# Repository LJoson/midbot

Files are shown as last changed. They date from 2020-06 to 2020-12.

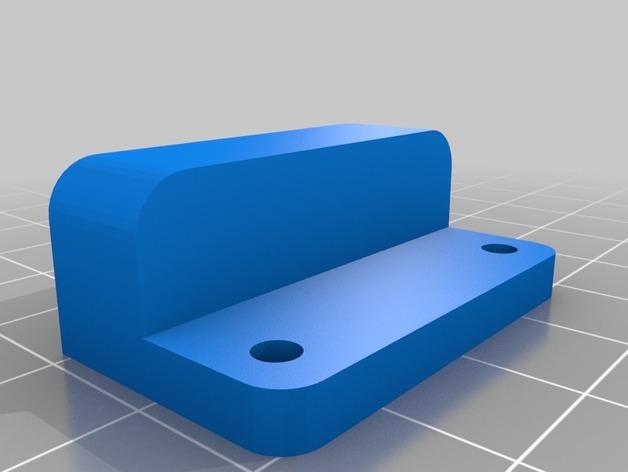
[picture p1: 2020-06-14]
midTbot/images/e1dbb92214a00844d0065ffd1623967f_preview_featured.jpg

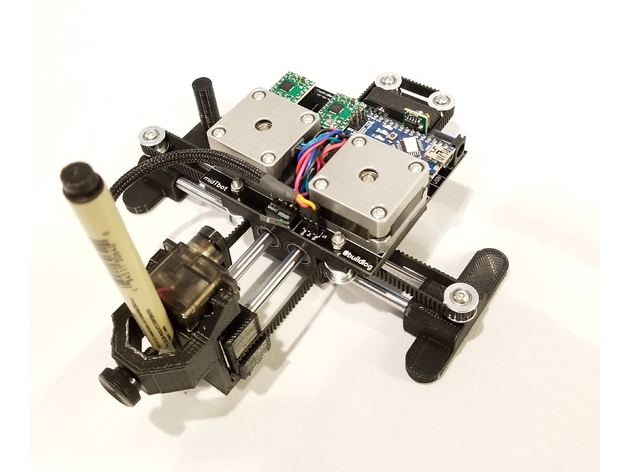
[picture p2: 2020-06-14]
midTbot打印件图纸.jpg

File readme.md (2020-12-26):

# 灵魂画手

## 结构
现在市面上有很多结构的写字机，而我要介绍的是经典的corexy结构的写字机。该写字机是基于T站上一个开源[写字机项目](https://www.thingiverse.com/thing:2587684).其结构如图：


<br/>
一般的corexy十字架构写字机两个电机是分开，其不好的一点就是太占空间，而midbot将两个控制电机集中在了中间，极大节省了空间。
另外想补充的是在我diy的过程中也发现几点可改进的地方
 - （1）底部支撑：不稳，容易倒
- （2）舵机抬笔：卡同步带地方易断裂,可以控制填充度，不易断裂或者改结构

## 工具
T站上控制主板多是esp32以及arduino nano,我使用的是arduino uno+cnc sheild控制器，控制算法就是经典的GRBL，网络上也有在stm32上移植grbl,我还没有实现，后面实现了进行补充。

所有资料获取：[https://github.com/LJoson/midbot](https://github.com/LJoson/midbot)

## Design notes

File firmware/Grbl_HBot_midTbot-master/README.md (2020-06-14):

# Grbl CNC for the MidTBot

This is a fork of Grbl 1.1f for the MidTBot. 

midTbot

The official Grbl Repo by Sungeon Jeon is [https://github.com/gnea/grbl](https://github.com/gnea/grbl).

This fork turns on the CoreXY functions, sets the correct defaults and adds pen up/down control of a hobby servo for the pen.

Any work coordinate system Z>0 is pen up. Any work coordinate system Z<=0 is pen down.

The MidTBot is documented on the [http://www.buildlog.net/blog/?s=midtbot](http://www.buildlog.net/blog/?s=midtbot). Please ask all question on the blog.

Note: This needs to be installed as an Arduino library.  See the [Grbl wiki pages](https://github.com/gnea/grbl/wiki/Compiling-Grbl) on how to do that.

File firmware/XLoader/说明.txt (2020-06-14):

本程序是吧PN（winAVR）编译成的  Grbl.hex   文件导入arduino的

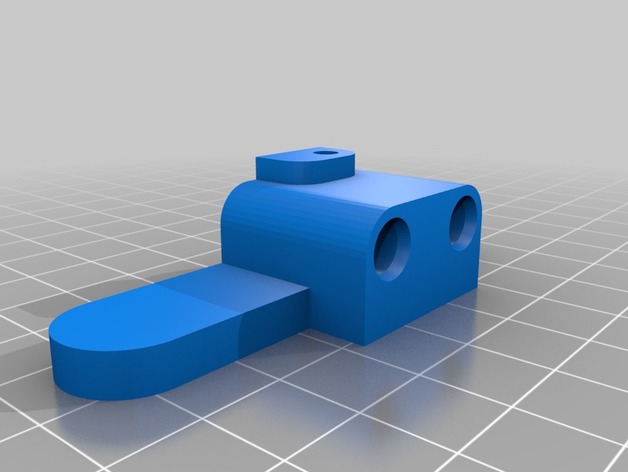
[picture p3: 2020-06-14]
midTbot/images/b2f7f5a82af39902b7f8d88fb1b9a30f_preview_featured.jpg

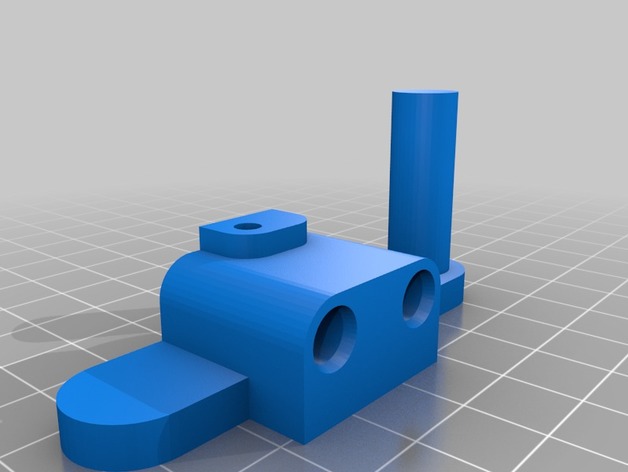
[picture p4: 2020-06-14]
midTbot/images/ceb36d84fa22627349a421942579ca87_preview_featured.jpg

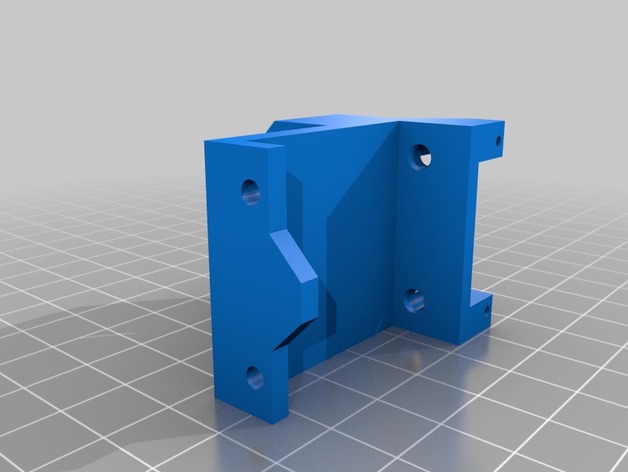
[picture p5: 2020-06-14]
midTbot/images/2167c671efe35847824a021b72f78122_preview_featured.jpg

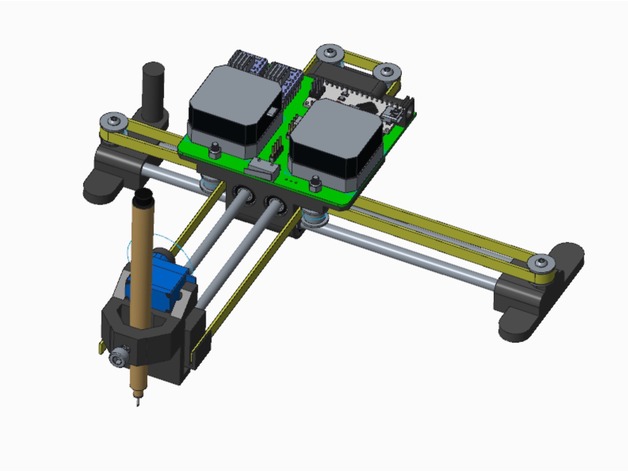
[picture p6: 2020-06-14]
midTbot/images/1ea54ba4b695a37cefbbd15caf575798_preview_featured.jpg

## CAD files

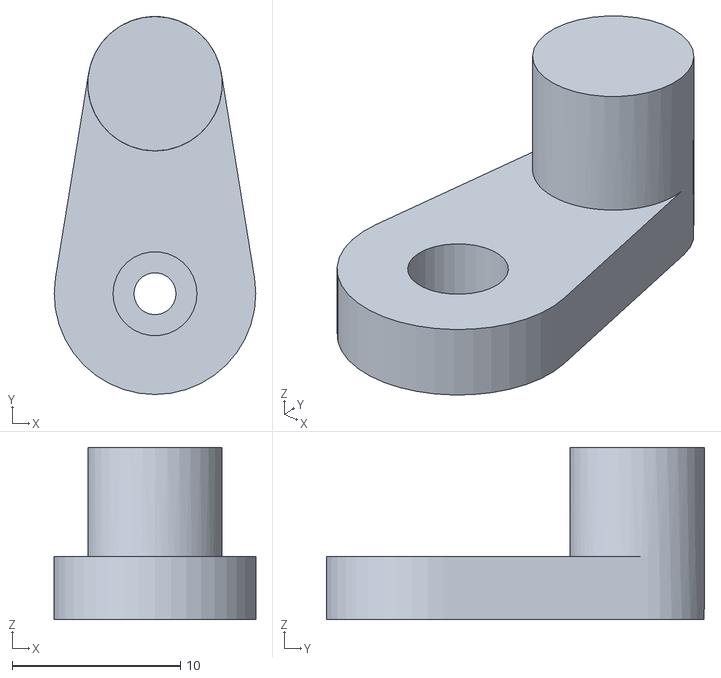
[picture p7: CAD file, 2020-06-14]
midTbot/files/midt_pen_lift_cam.stl
12.0 x 22.5 x 10.2

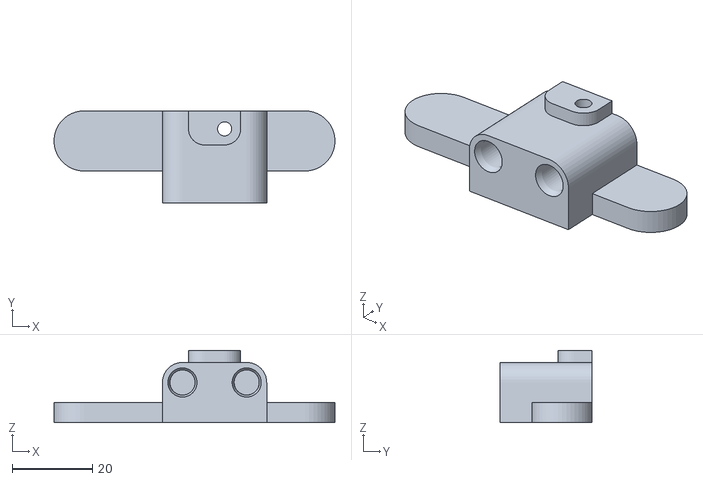
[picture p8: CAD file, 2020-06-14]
midTbot/files/midt_right_foot.stl
70.0 x 23.0 x 18.0

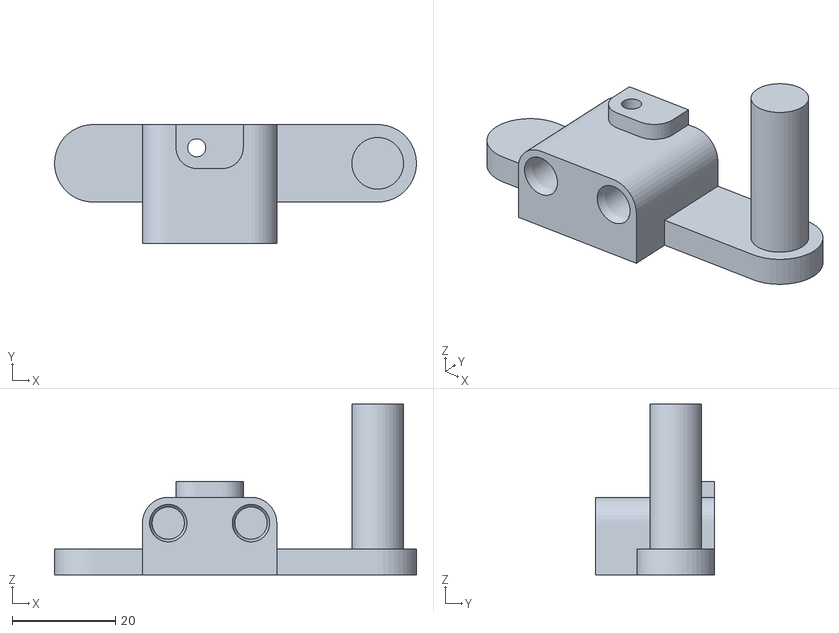
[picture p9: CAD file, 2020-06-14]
midTbot/files/midt_left_foot.stl
70.0 x 23.0 x 33.0

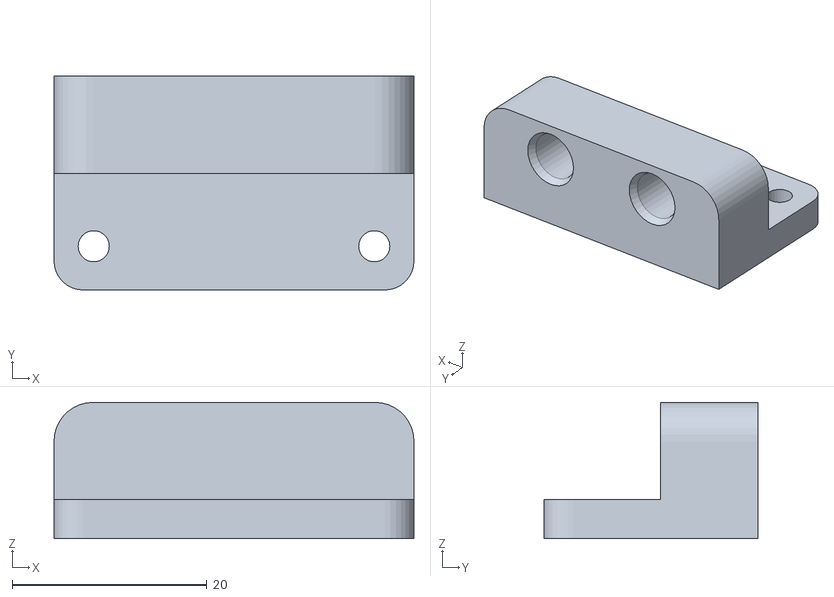
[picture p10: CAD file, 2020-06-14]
midTbot/files/midt_tailblock.stl
37.0 x 22.0 x 14.0

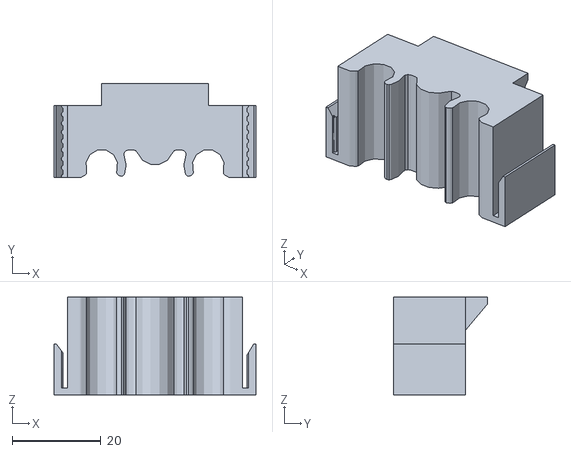
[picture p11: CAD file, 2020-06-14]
midTbot/files/midt-headblock.stl
45.5 x 21.2 x 22.0

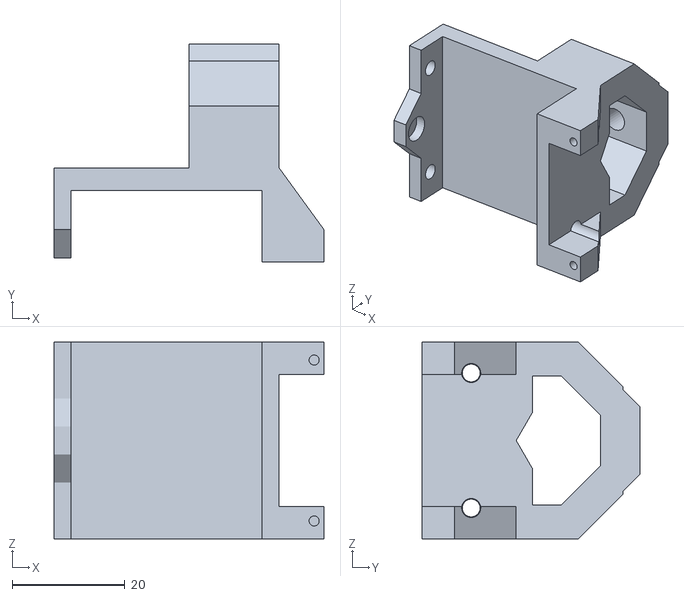
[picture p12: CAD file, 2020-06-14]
midTbot/files/midtbot_pen_carriage.stl
48.0 x 38.8 x 35.0

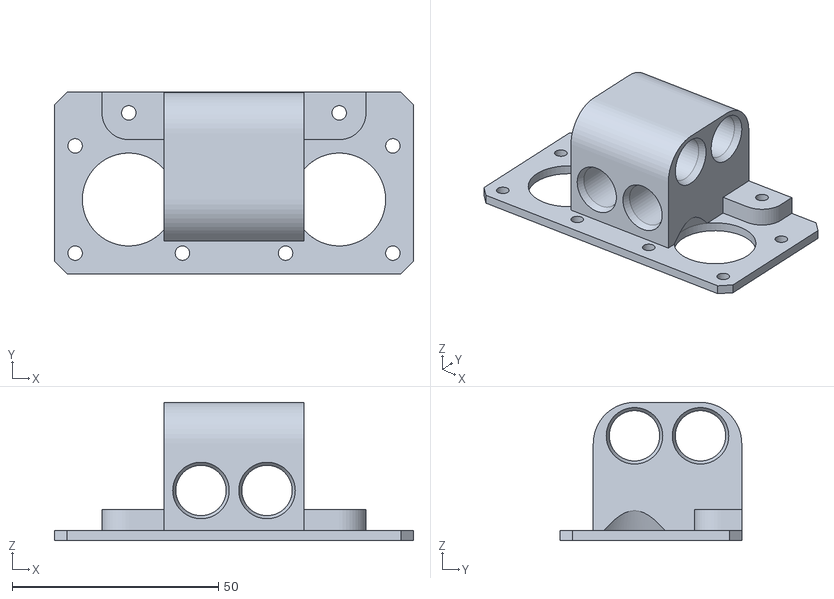
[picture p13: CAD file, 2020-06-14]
midTbot/files/midt_carriage_block.stl
87.0 x 44.0 x 33.5

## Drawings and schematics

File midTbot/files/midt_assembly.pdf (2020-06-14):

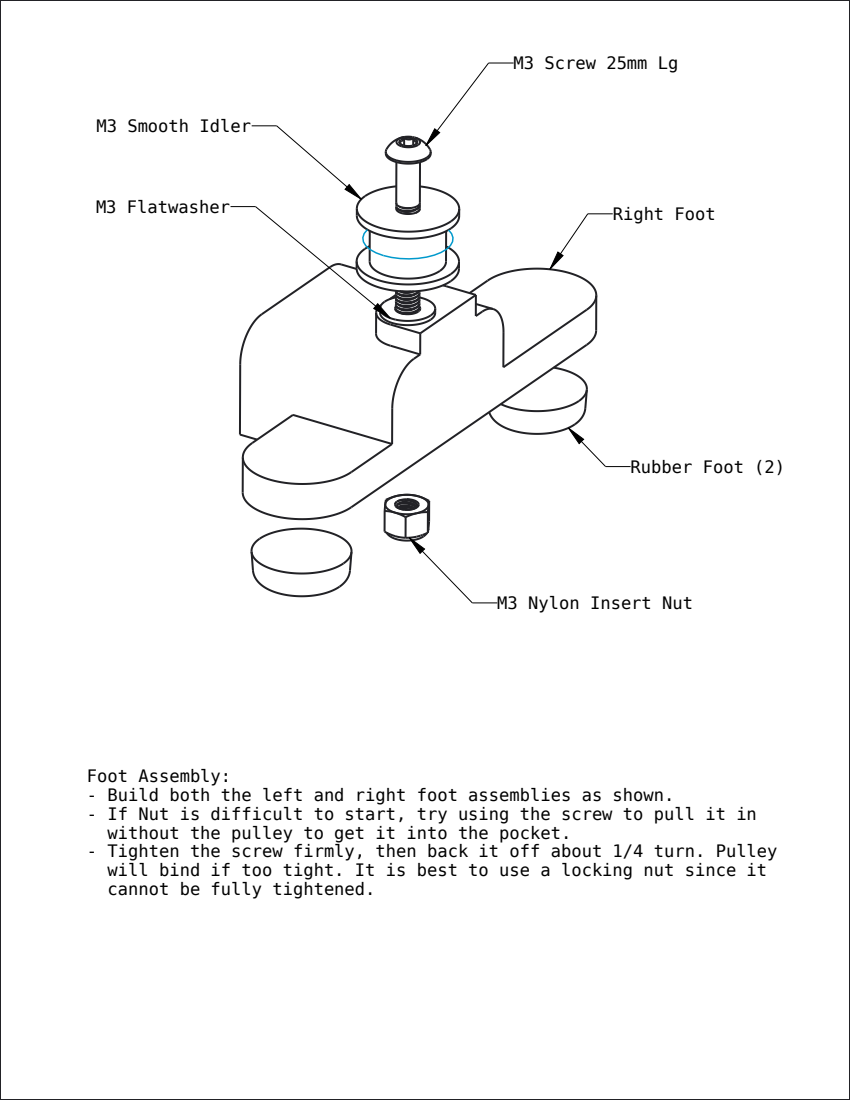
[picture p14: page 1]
Rubber Foot (2); M3 Screw 25mm Lg; M3 Smooth Idler

Right Foot M3 Flatwasher

M3 Nylon Insert Nut

Foot Assembly:
- Build both the left and right foot assemblies as shown.
- If Nut is difficult to start, try using the screw to pull it in
without the pulley to get it into the pocket.
- Tighten the screw firmly, then back it off about 1/4 turn. Pulley
will bind if too tight. It is best to use a locking nut since it
cannot be fully tightened.

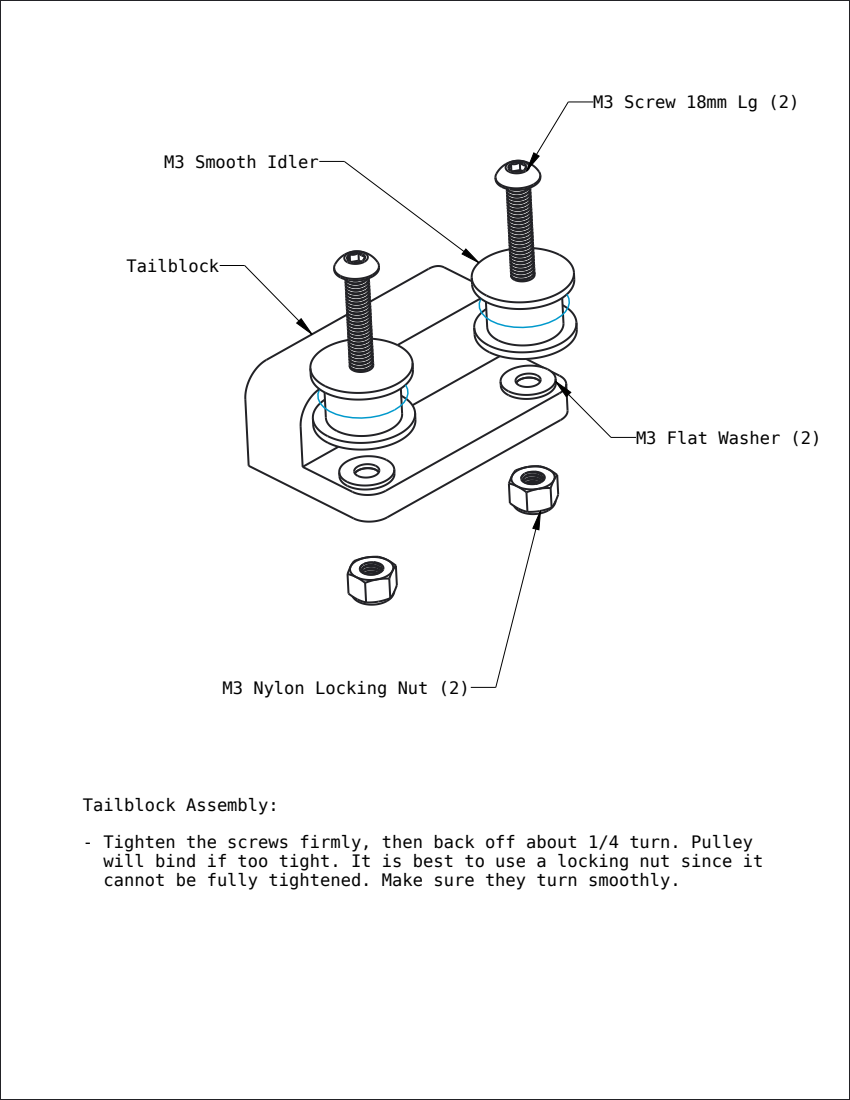
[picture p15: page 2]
Tailblock; M3 Screw 18mm Lg (2); M3 Flat Washer (2); M3 Smooth Idler

M3 Nylon Locking Nut (2)

Tailblock Assembly:
- Tighten the screws firmly, then back off about 1/4 turn. Pulley
will bind if too tight. It is best to use a locking nut since it
cannot be fully tightened. Make sure they turn smoothly.

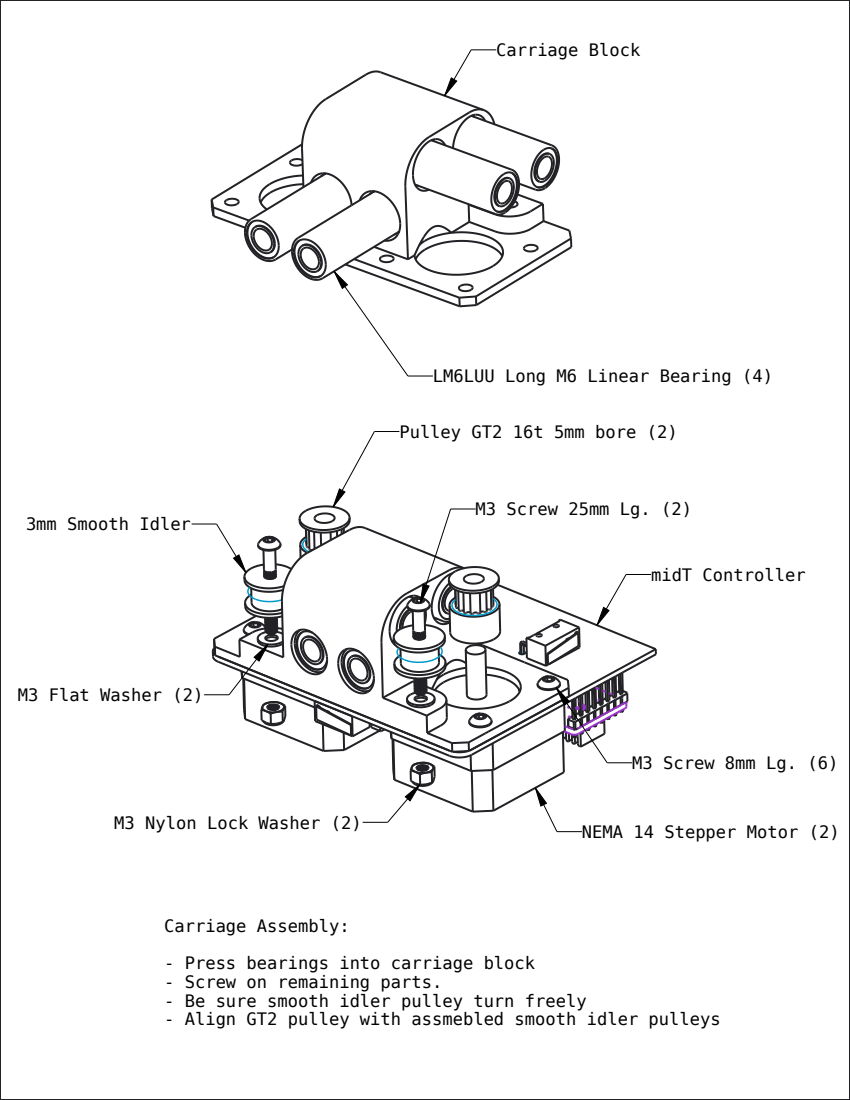
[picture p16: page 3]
Carriage Block; midT Controller; Pulley GT2 16t 5mm bore (2); 3mm Smooth Idler; M3 Flat Washer (2); M3 Screw 25mm Lg. (2); M3 Screw 8mm Lg. (6)

LM6LUU Long M6 Linear Bearing (4)

M3 Nylon Lock Washer (2)

NEMA 14 Stepper Motor (2)

Carriage Assembly:
- Press bearings into carriage block
- Screw on remaining parts.
- Be sure smooth idler pulley turn freely
- Align GT2 pulley with assmebled smooth idler pulleys

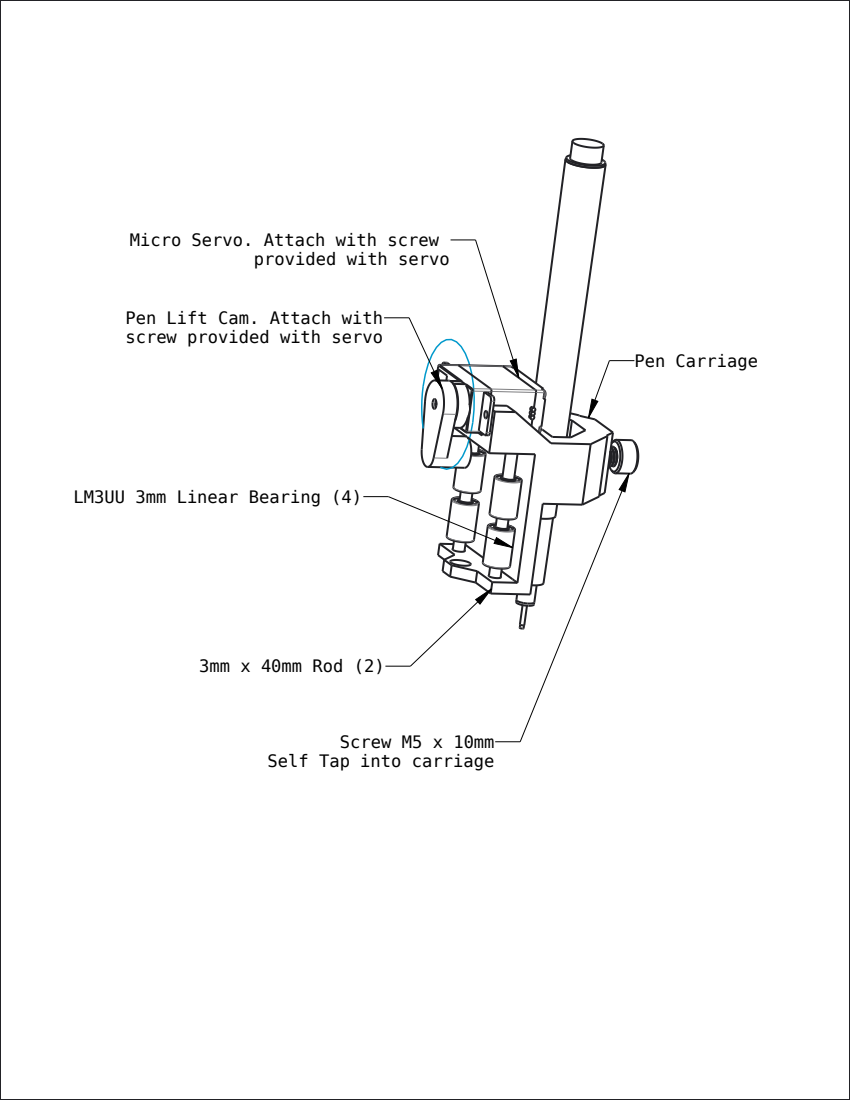
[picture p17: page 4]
Pen Carriage; 3mm x 40mm Rod (2); LM3UU 3mm Linear Bearing (4); Screw M5 x 10mm

Micro Servo. Attach with screw

provided with servo

Pen Lift Cam. Attach with
screw provided with servo

Self Tap into carriage

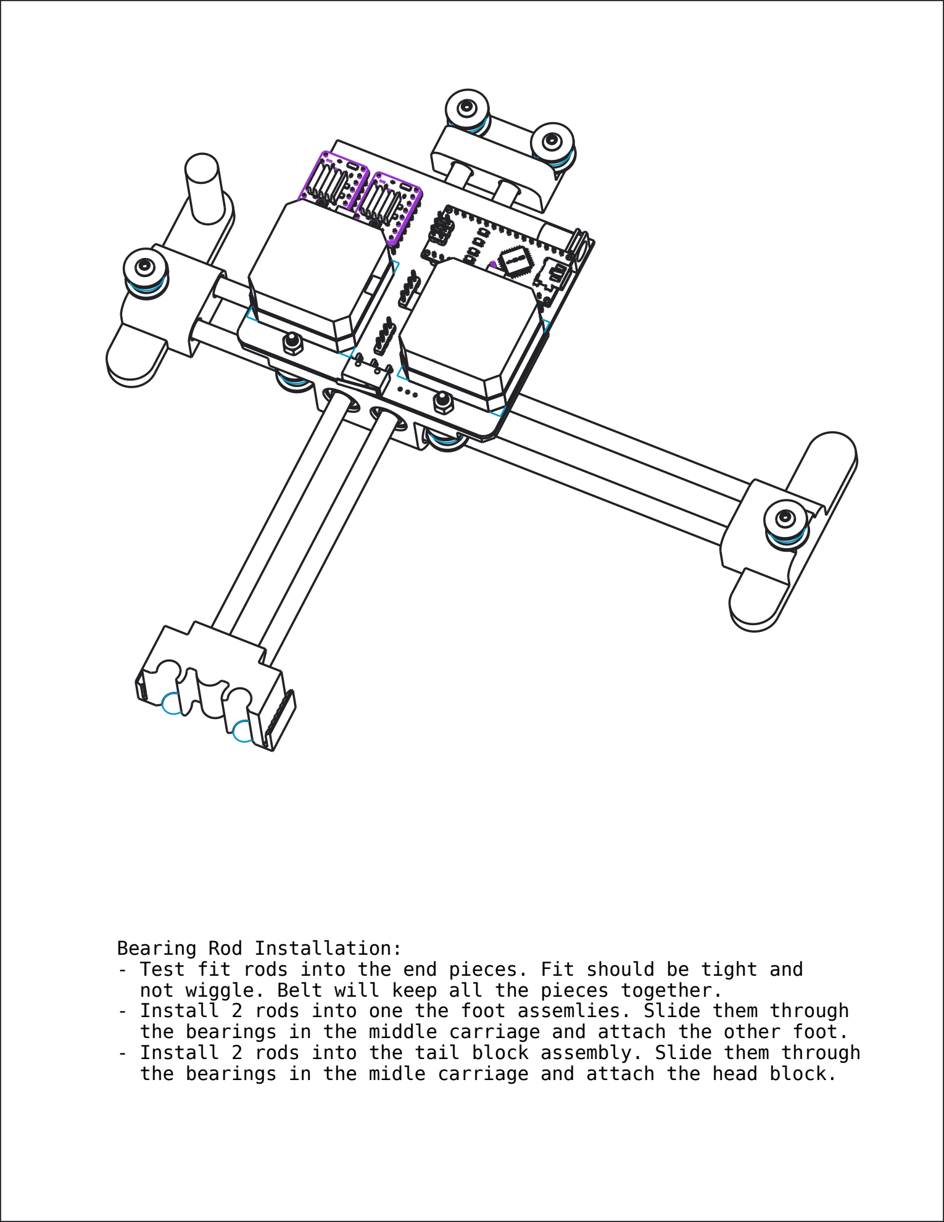
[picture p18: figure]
Bearing Rod Installation:

- Test fit rods into the end pieces. Fit should be tight and not wiggle. Belt will keep all the pieces together.
- Install 2 rods into one the foot assemlies. Slide them through the bearings in the middle carriage and attach the other foot.
- Install 2 rods into the tail block assembly. Slide them through the bearings in the midle carriage and attach the head block.

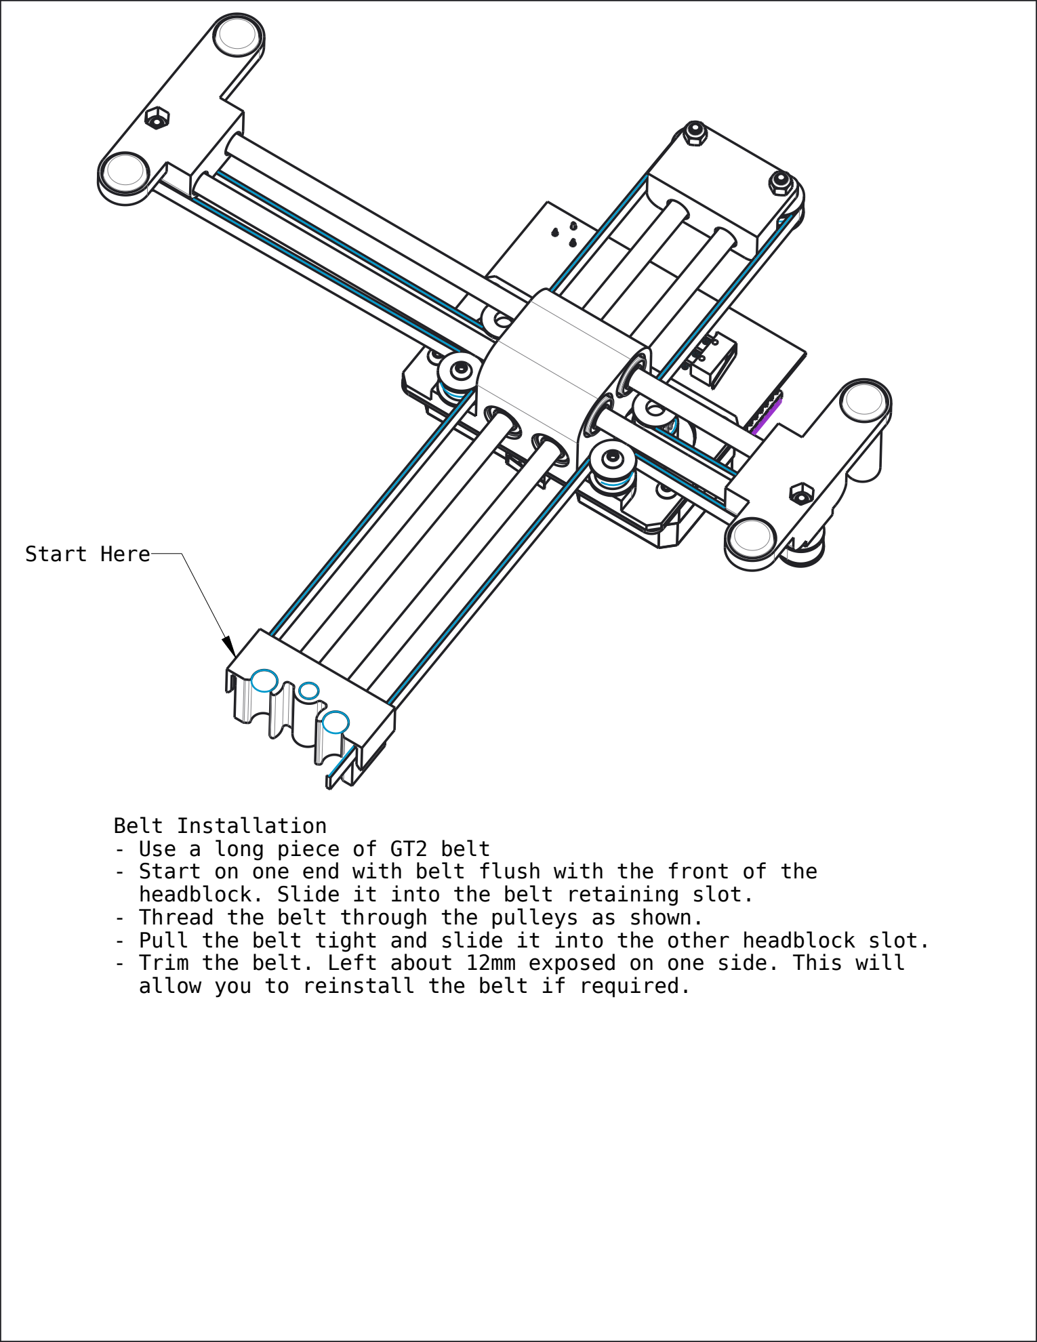
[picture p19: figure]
Belt Installation - Use a long piece of GT2 belt; Start Here

- Start on one end with belt flush with the front of the headblock. Slide it into the belt retaining slot.
- Thread the belt through the pulleys as shown.
- Pull the belt tight and slide it into the other headblock slot.
- Trim the belt. Left about 12mm exposed on one side. This will allow you to reinstall the belt if required.

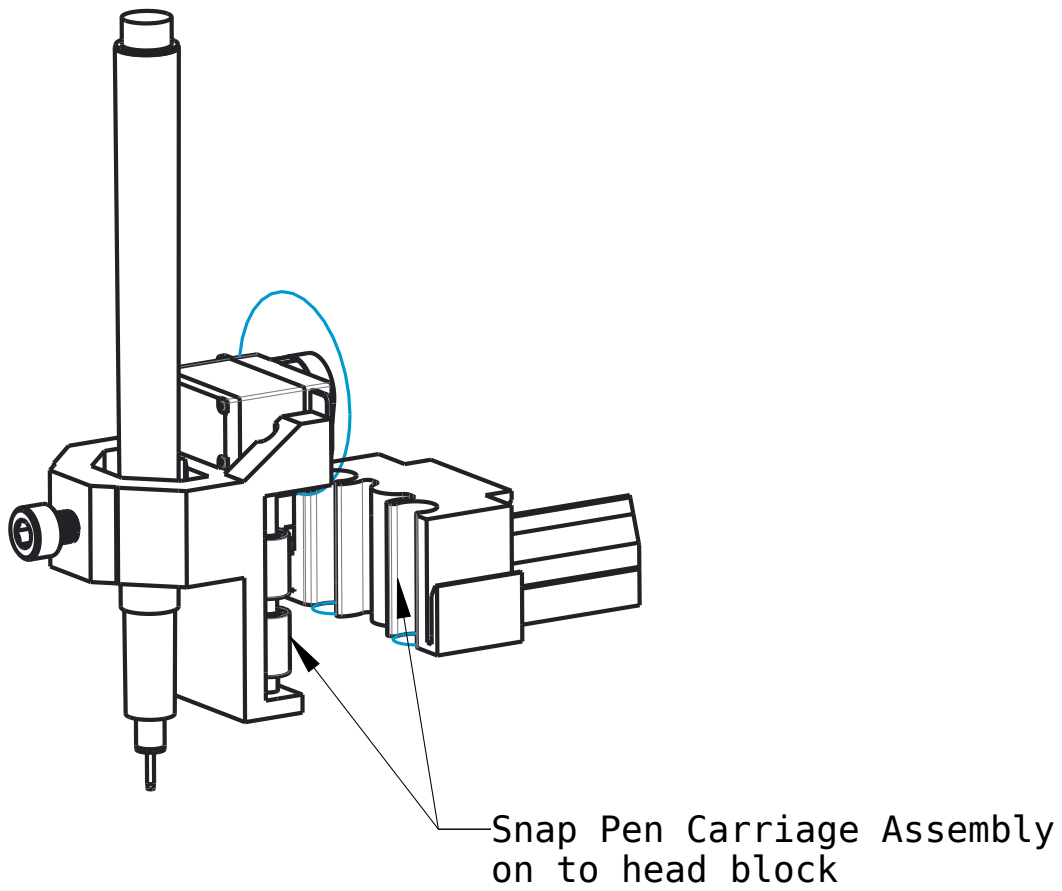
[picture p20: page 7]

Snap Pen Carriage Assembly
on to head block

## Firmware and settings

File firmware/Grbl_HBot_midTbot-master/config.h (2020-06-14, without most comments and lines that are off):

#define config_h
#include "grbl.h" // For Arduino IDE compatibility.
#define DEFAULTS_MIDTBOT
#define CPU_MAP_ATMEGA328P_SERVO // Arduino Uno CPU
#define BAUD_RATE 115200
#define CMD_RESET 0x18 // ctrl-x.
#define CMD_STATUS_REPORT '?'
#define CMD_CYCLE_START '~'
#define CMD_FEED_HOLD '!'
#define CMD_SAFETY_DOOR 0x84
#define CMD_JOG_CANCEL  0x85
#define CMD_DEBUG_REPORT 0x86 // Only when DEBUG enabled, sends debug report in '{}' braces.
#define CMD_FEED_OVR_RESET 0x90         // Restores feed override value to 100%.
#define CMD_FEED_OVR_COARSE_PLUS 0x91
#define CMD_FEED_OVR_COARSE_MINUS 0x92
#define CMD_FEED_OVR_FINE_PLUS  0x93
#define CMD_FEED_OVR_FINE_MINUS  0x94
#define CMD_RAPID_OVR_RESET 0x95        // Restores rapid override value to 100%.
#define CMD_RAPID_OVR_MEDIUM 0x96
#define CMD_RAPID_OVR_LOW 0x97
#define CMD_SPINDLE_OVR_RESET 0x99      // Restores spindle override value to 100%.
#define CMD_SPINDLE_OVR_COARSE_PLUS 0x9A
#define CMD_SPINDLE_OVR_COARSE_MINUS 0x9B
#define CMD_SPINDLE_OVR_FINE_PLUS 0x9C
#define CMD_SPINDLE_OVR_FINE_MINUS 0x9D
#define CMD_SPINDLE_OVR_STOP 0x9E
#define CMD_COOLANT_FLOOD_OVR_TOGGLE 0xA0
#define CMD_COOLANT_MIST_OVR_TOGGLE 0xA1
#define HOMING_INIT_LOCK // Comment to disable
#define HOMING_CYCLE_0 (1<<X_AXIS)  // COREXY COMPATIBLE: First home X
#define HOMING_CYCLE_1 (1<<Y_AXIS)  // COREXY COMPATIBLE: Then home Y
#define N_HOMING_LOCATE_CYCLE 1 // Integer (1-128)
#define N_STARTUP_LINE 2 // Integer (1-2)
#define N_DECIMAL_COORDVALUE_INCH 4 // Coordinate or position value in inches
#define N_DECIMAL_COORDVALUE_MM   3 // Coordinate or position value in mm
#define N_DECIMAL_RATEVALUE_INCH  1 // Rate or velocity value in in/min
#define N_DECIMAL_RATEVALUE_MM    0 // Rate or velocity value in mm/min
#define N_DECIMAL_SETTINGVALUE    3 // Decimals for floating point setting values
#define N_DECIMAL_RPMVALUE        0 // RPM value in rotations per min.
#define MESSAGE_PROBE_COORDINATES // Enabled by default. Comment to disable.
#define SAFETY_DOOR_SPINDLE_DELAY 4.0 // Float (seconds)
#define SAFETY_DOOR_COOLANT_DELAY 1.0 // Float (seconds)
#define COREXY // Default disabled. Uncomment to enable.
#define CHECK_LIMITS_AT_INIT
#define DEFAULT_FEED_OVERRIDE           100 // 100%. Don't change this value.
#define MAX_FEED_RATE_OVERRIDE          200 // Percent of programmed feed rate (100-255). Usually 120% or 200%
#define MIN_FEED_RATE_OVERRIDE           10 // Percent of programmed feed rate (1-100). Usually 50% or 1%
#define FEED_OVERRIDE_COARSE_INCREMENT   10 // (1-99). Usually 10%.
#define FEED_OVERRIDE_FINE_INCREMENT      1 // (1-99). Usually 1%.
#define DEFAULT_RAPID_OVERRIDE  100 // 100%. Don't change this value.
#define RAPID_OVERRIDE_MEDIUM    50 // Percent of rapid (1-99). Usually 50%.
#define RAPID_OVERRIDE_LOW       25 // Percent of rapid (1-99). Usually 25%.
#define DEFAULT_SPINDLE_SPEED_OVERRIDE    100 // 100%. Don't change this value.
#define MAX_SPINDLE_SPEED_OVERRIDE        200 // Percent of programmed spindle speed (100-255). Usually 200%.
#define MIN_SPINDLE_SPEED_OVERRIDE         10 // Percent of programmed spindle speed (1-100). Usually 10%.
#define SPINDLE_OVERRIDE_COARSE_INCREMENT  10 // (1-99). Usually 10%.
#define SPINDLE_OVERRIDE_FINE_INCREMENT     1 // (1-99). Usually 1%.
#define RESTORE_OVERRIDES_AFTER_PROGRAM_END // Default enabled. Comment to disable.
#define REPORT_FIELD_PIN_STATE // Default enabled. Comment to disable.
#define REPORT_FIELD_WORK_COORD_OFFSET // Default enabled. Comment to disable.
#define REPORT_FIELD_OVERRIDES // Default enabled. Comment to disable.
#define REPORT_FIELD_LINE_NUMBERS // Default enabled. Comment to disable.
#define REPORT_OVR_REFRESH_BUSY_COUNT 20  // (1-255)
#define REPORT_OVR_REFRESH_IDLE_COUNT 10  // (1-255) Must be less than or equal to the busy count
#define REPORT_WCO_REFRESH_BUSY_COUNT 30  // (2-255)
#define REPORT_WCO_REFRESH_IDLE_COUNT 10  // (2-255) Must be less than or equal to the busy count
#define ACCELERATION_TICKS_PER_SECOND 100
#define ADAPTIVE_MULTI_AXIS_STEP_SMOOTHING  // Default enabled. Comment to disable.
#define TOOL_LENGTH_OFFSET_AXIS Z_AXIS // Default z-axis. Valid values are X_AXIS, Y_AXIS, or Z_AXIS.
#define MINIMUM_JUNCTION_SPEED 0.0 // (mm/min)
#define MINIMUM_FEED_RATE 1.0 // (mm/min)
#define N_ARC_CORRECTION 12 // Integer (1-255)
#define ARC_ANGULAR_TRAVEL_EPSILON 5E-7 // Float (radians)
#define DWELL_TIME_STEP 50 // Integer (1-255) (milliseconds)
#define ENABLE_RESTORE_EEPROM_WIPE_ALL         // '$RST=*' Default enabled. Comment to disable.
#define ENABLE_RESTORE_EEPROM_DEFAULT_SETTINGS // '$RST=$' Default enabled. Comment to disable.
#define ENABLE_RESTORE_EEPROM_CLEAR_PARAMETERS // '$RST=#' Default enabled. Comment to disable.
#define ENABLE_BUILD_INFO_WRITE_COMMAND // '$I=' Default enabled. Comment to disable.
#define FORCE_BUFFER_SYNC_DURING_EEPROM_WRITE // Default enabled. Comment to disable.
#define FORCE_BUFFER_SYNC_DURING_WCO_CHANGE // Default enabled. Comment to disable.
#define PARKING_AXIS Z_AXIS // Define which axis that performs the parking motion
#define PARKING_TARGET -5.0 // Parking axis target. In mm, as machine coordinate [-max_travel,0].
#define PARKING_RATE 500.0 // Parking fast rate after pull-out in mm/min.
#define PARKING_PULLOUT_RATE 100.0 // Pull-out/plunge slow feed rate in mm/min.
#define PARKING_PULLOUT_INCREMENT 5.0 // Spindle pull-out and plunge distance in mm. Incremental distance.
#define N_PIECES 4  // Integer (1-4). Number of piecewise lines used in script solution.
#define RPM_MAX  11686.4  // Max RPM of model. $30 > RPM_MAX will be limited to RPM_MAX.
#define RPM_MIN  202.5    // Min RPM of model. $31 < RPM_MIN will be limited to RPM_MIN.
#define RPM_POINT12  6145.4  // Used N_PIECES >=2. Junction point between lines 1 and 2.
#define RPM_POINT23  9627.8  // Used N_PIECES >=3. Junction point between lines 2 and 3.
#define RPM_POINT34  10813.9 // Used N_PIECES = 4. Junction point between lines 3 and 4.
#define RPM_LINE_A1  3.197101e-03  // Used N_PIECES >=1. A and B constants of line 1.
#define RPM_LINE_B1  -3.526076e-1
#define RPM_LINE_A2  1.722950e-2   // Used N_PIECES >=2. A and B constants of line 2.
#define RPM_LINE_B2  8.588176e+01
#define RPM_LINE_A3  5.901518e-02  // Used N_PIECES >=3. A and B constants of line 3.
#define RPM_LINE_B3  4.881851e+02
#define RPM_LINE_A4  1.203413e-01  // Used N_PIECES = 4. A and B constants of line 4.
#define RPM_LINE_B4  1.151360e+03

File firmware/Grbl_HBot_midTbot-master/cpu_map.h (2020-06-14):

/*
  cpu_map.h - CPU and pin mapping configuration file
  Part of Grbl

  Copyright (c) 2012-2016 Sungeun K. Jeon for Gnea Research LLC

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
  You should have received a copy of the GNU General Public License
  along with Grbl.  If not, see <http://www.gnu.org/licenses/>.
*/

/* The cpu_map.h files serve as a central pin mapping selection file for different
   processor types or alternative pin layouts. This version of Grbl officially supports
   only the Arduino Mega328p. */


#ifndef cpu_map_h
#define cpu_map_h


#ifdef CPU_MAP_ATMEGA328P_SERVO 

  // Define serial port pins and interrupt vectors.
  #define SERIAL_RX     USART_RX_vect
  #define SERIAL_UDRE   USART_UDRE_vect

  // Define step pulse output pins. NOTE: All step bit pins must be on the same port.
  #define STEP_DDR        DDRD
  #define STEP_PORT       PORTD
  #define X_STEP_BIT      2  // Uno Digital Pin 2
  #define Y_STEP_BIT      3  // Uno Digital Pin 3
  #define Z_STEP_BIT      4  // Uno Digital Pin 4
  #define STEP_MASK       ((1<<X_STEP_BIT)|(1<<Y_STEP_BIT)|(1<<Z_STEP_BIT)) // All step bits

  // Define step direction output pins. NOTE: All direction pins must be on the same port.
  #define DIRECTION_DDR     DDRD
  #define DIRECTION_PORT    PORTD
  #define X_DIRECTION_BIT   5  // Uno Digital Pin 5
  #define Y_DIRECTION_BIT   6  // Uno Digital Pin 6
  #define Z_DIRECTION_BIT   7  // Uno Digital Pin 7
  #define DIRECTION_MASK    ((1<<X_DIRECTION_BIT)|(1<<Y_DIRECTION_BIT)|(1<<Z_DIRECTION_BIT)) // All direction bits

  // Define stepper driver enable/disable output pin.
  #define STEPPERS_DISABLE_DDR    DDRB
  #define STEPPERS_DISABLE_PORT   PORTB
  #define STEPPERS_DISABLE_BIT    0  // Uno Digital Pin 8
  #define STEPPERS_DISABLE_MASK   (1<<STEPPERS_DISABLE_BIT)

  // Define homing/hard limit switch input pins and limit interrupt vectors.
  // NOTE: All limit bit pins must be on the same port, but not on a port with other input pins (CONTROL).
  #define LIMIT_DDR        DDRB
  #define LIMIT_PIN        PINB
  #define LIMIT_PORT       PORTB
  #define X_LIMIT_BIT      1  // Uno Digital Pin 9
  #define Y_LIMIT_BIT      2  // Uno Digital Pin 10  
  #define Z_LIMIT_BIT	   4 // Uno Digital Pin 12
  
  
  #define LIMIT_MASK       ((1<<X_LIMIT_BIT)|(1<<Y_LIMIT_BIT)|(1<<Z_LIMIT_BIT)) // All limit bits
  #define LIMIT_INT        PCIE0  // Pin change interrupt enable pin
  #define LIMIT_INT_vect   PCINT0_vect
  #define LIMIT_PCMSK      PCMSK0 // Pin change interrupt register

  // Define spindle enable and spindle direction output pins.
  #define SPINDLE_ENABLE_DDR    DDRB
  #define SPINDLE_ENABLE_PORT   PORTB
  // Z Limit pin and spindle PWM/enable pin swapped to access hardware PWM on Pin 11.
  
  #define SPINDLE_ENABLE_BIT    5  // Nano Digital Pin 13
  
  // Define flood and mist coolant enable output pins.
  #define COOLANT_FLOOD_DDR   DDRC
  #define COOLANT_FLOOD_PORT  PORTC
  #define COOLANT_FLOOD_BIT   3  // Uno Analog Pin 3
  #define COOLANT_MIST_DDR   DDRC
  #define COOLANT_MIST_PORT  PORTC
  #define COOLANT_MIST_BIT   4  // Uno Analog Pin 4

  // Define user-control controls (cycle start, reset, feed hold) input pins.
  // NOTE: All CONTROLs pins must be on the same port and not on a port with other input pins (limits).
  #define CONTROL_DDR       DDRC
  #define CONTROL_PIN       PINC
  #define CONTROL_PORT      PORTC
  #define CONTROL_RESET_BIT         0  // Uno Analog Pin 0
  #define CONTROL_FEED_HOLD_BIT     1  // Uno Analog Pin 1
  #define CONTROL_CYCLE_START_BIT   2  // Uno Analog Pin 2
  #define CONTROL_SAFETY_DOOR_BIT   1  // Uno Analog Pin 1 NOTE: Safety door is shared with feed hold. Enabled by config define.
  #define CONTROL_INT       PCIE1  // Pin change interrupt enable pin
  #define CONTROL_INT_vect  PCINT1_vect
  #define CONTROL_PCMSK     PCMSK1 // Pin change interrupt register
  #define CONTROL_MASK      ((1<<CONTROL_RESET_BIT)|(1<<CONTROL_FEED_HOLD_BIT)|(1<<CONTROL_CYCLE_START_BIT)|(1<<CONTROL_SAFETY_DOOR_BIT))
  #define CONTROL_INVERT_MASK   CONTROL_MASK // May be re-defined to only invert certain control pins.

  // Define probe switch input pin.
  #define PROBE_DDR       DDRC
  #define PROBE_PIN       PINC
  #define PROBE_PORT      PORTC
  #define PROBE_BIT       5  // Uno Analog Pin 5
  #define PROBE_MASK      (1<<PROBE_BIT)

  // Variable spindle configuration below. Do not change unless you know what you are doing.
  // NOTE: Only used when variable spindle is enabled.
  #define SPINDLE_PWM_MAX_VALUE     255 // Don't change. 328p fast PWM mode fixes top value as 255.
  #ifndef SPINDLE_PWM_MIN_VALUE
    #define SPINDLE_PWM_MIN_VALUE   1   // Must be greater than zero.
  #endif
  #define SPINDLE_PWM_OFF_VALUE     0
  #define SPINDLE_PWM_RANGE         (SPINDLE_PWM_MAX_VALUE-SPINDLE_PWM_MIN_VALUE)
  #define SPINDLE_TCCRA_REGISTER	  TCCR2A
  #define SPINDLE_TCCRB_REGISTER	  TCCR2B
  #define SPINDLE_OCR_REGISTER      OCR2A
  #define SPINDLE_COMB_BIT	        COM2A1

  // Prescaled, 8-bit Fast PWM mode.
  #define SPINDLE_TCCRA_INIT_MASK   ((1<<WGM20) | (1<<WGM21))  // Configures fast PWM mode.
  // #define SPINDLE_TCCRB_INIT_MASK   (1<<CS20)               // Disable prescaler -> 62.5kHz
  // #define SPINDLE_TCCRB_INIT_MASK   (1<<CS21)               // 1/8 prescaler -> 7.8kHz (Used in v0.9)
  // #define SPINDLE_TCCRB_INIT_MASK   ((1<<CS21) | (1<<CS20)) // 1/32 prescaler -> 1.96kHz
  #define SPINDLE_TCCRB_INIT_MASK      (1<<CS22)               // 1/64 prescaler -> 0.98kHz (J-tech laser)

  // NOTE: On the 328p, these must be the same as the SPINDLE_ENABLE settings.
  #define SPINDLE_PWM_DDR	  DDRB
  #define SPINDLE_PWM_PORT  PORTB
  #define SPINDLE_PWM_BIT	  3    // Uno Digital Pin 11

#endif

/*
#ifdef CPU_MAP_CUSTOM_PROC
  // For a custom pin map or different processor, copy and edit one of the available cpu
  // map files and modify it to your needs. Make sure the defined name is also changed in
  // the config.h file.
#endif
*/

#endif

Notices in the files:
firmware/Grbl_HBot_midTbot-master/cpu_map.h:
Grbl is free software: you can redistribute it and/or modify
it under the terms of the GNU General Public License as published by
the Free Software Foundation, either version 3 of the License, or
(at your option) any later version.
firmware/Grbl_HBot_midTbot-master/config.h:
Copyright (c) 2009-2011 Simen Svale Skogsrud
